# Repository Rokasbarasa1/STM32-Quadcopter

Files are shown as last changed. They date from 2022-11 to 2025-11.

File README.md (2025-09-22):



I am making a quadcopter from scratch (firmware including). This is the second step after my [Self balancing robot](https://github.com/Rokasbarasa1/ESP32-self-balancing-robot) project. It is still a work in progress, but a lot of the heavy lifting has already been done.

### Some features:
* Acro and Angle modes.
* GPS position hold flight mode (Work in progress).
* Altitude hold flight mode (Work in progress).
* Controled by my custom [Pi-pico based remote control](https://github.com/Rokasbarasa1/Pi-Pico-remote-control). 

### Sensors and hardware used for controller:
* Controller mcu - STM32F411
* Accelerometer + Gyro - MPU6050
* Magnetometer - MMC5603 (Used QMC5883 before)
* GPS - HGLRC M100 5883 (Used BN357 before)
* Barometer - MS5611 (Used BMP280 before)
* Radio link - RadioMaster RP1 2.4GHz ELRS (Work in progress)
* Debug Radio communication - NRF24l01
* Logging - [My custom STM32F411 based SD Logger](https://github.com/Rokasbarasa1/Logger). 

### Hardware of the drone itself:
* Motors - 4 x EMAX ECO II Series 2807 Motor
* ESC's - 4 x HGLRC 30amp 3-5S Dshot600 BLHeli_S 16.5 BB2 ESC (F-H-40 flashed with BlueJay 0.21.0V for BDshot600)
* Proppelers - 4 x HQProp DP 7x3.5x3 V1S 3 blade Propeller
* Battery - CNHL Black Series 3200mAh 14.8V 30C 4S (also used Turnigy 2200mAh 3S 25C)

# Latest flight video (January 2025)

Watch the video (https://www.youtube.com/watch?v=jI-Cl2vByNU)

# Pictures (Outdated)
Frame top
Frame bottom
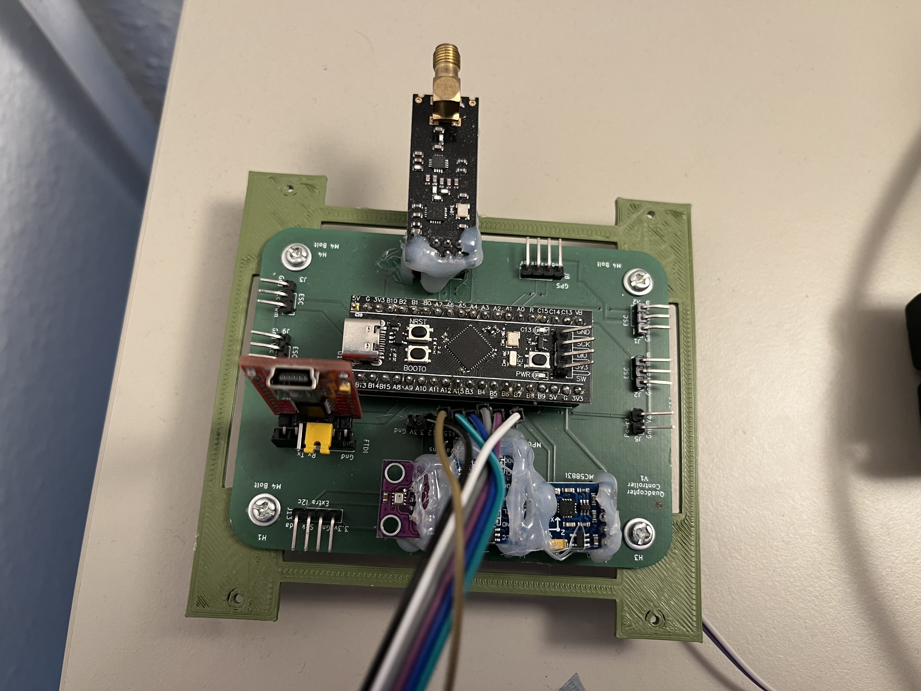
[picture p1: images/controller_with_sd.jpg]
Controller


### Checklist for going testing
* Drone frame
* Controller
* Controller antenna
* Propellers
* Sd card adapter
* Micro sd card
* Pliers 
* Wire cutters
* Screwdriver 
* Screwdriver bits
* Remote control
* Laptop
* Usb extension cable
* STM32 programmer
* Charged battery
* Battery checker

# Design documentation (work in progress)

## Code diagram

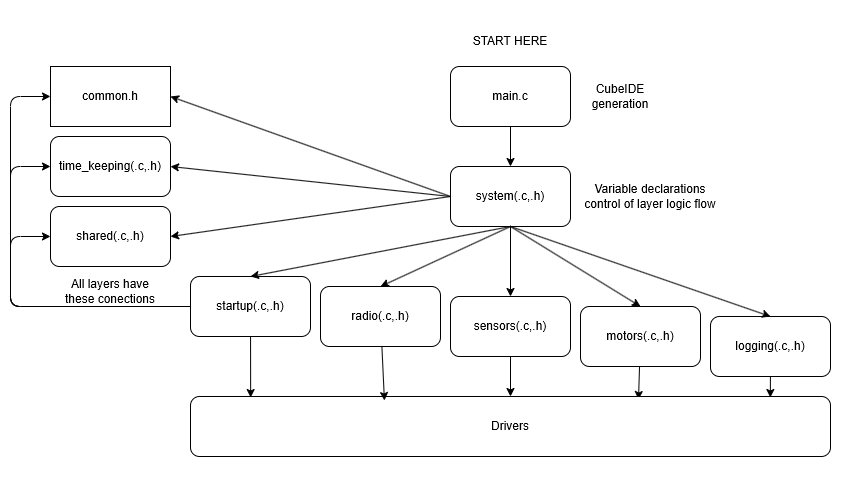
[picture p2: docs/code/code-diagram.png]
Code diagram


## Controller 

The controller is the main piece of the system. It is much more limited in what it can do than a normal computer, it is smaller, slower and resource constrained. So it cannot run a full GUI operating system. The good thing about them is that they are cheap and, depending on which one you get, just powerful enough to do interesting things. They are also cheap, I got mine for 7.28 USD. The microcontroller itself is just a chip on the breadboard. It is very self sufficient, sometimes you can just supply them stable power and they work fine. Like the attiny85 that just plugs into a breadboard. 

We need one that is more powerful than that so we will go with one called the STM32F411. ST(M)icroelectronics is the manufacturer, the 32 bit is how big data chunks the system can handle, and the F stands mainstream performance line of their chips, 411 is just a serial number for features. We dont really care about the features that much, it is maninstream so it will work for most things. 

I went with a ST microcontroller as it was one I had not used before. The chip on this one is very small so it is mounted on a pcb to seperate the tiny pins on the chip into big pins that we can use. The PCB that it is mounted on gives the microcontroller name blackpill because its a black pcb and its small. The pcb also has some extra features like voltage regulators to protect the chip, external oscillators to speed it up and leds to help us indicate status later. The pcb is so small that it lacks some quality of life features that a big pcb would have, like a programmer. The chip has to instead be programmed usng another product of ST called ST-link V2, which just converts a Usb interface to a programming interface for the stm32, it uses 4 pins to do that. This is negative of ST's products, other manufacturers dont have this problem with small pcb's, most of the time. The upside is you can debug the code with the same product, this is something that is painful on other microcontroller brands. The small form factor of the pcb is also very helpful for integrating the microcontroller into projects.

Each microcontroller manufacturer has their own "library" that abstracts the difficullt hardware drivers (HAL), on top of which the coding of the microcontroller can be done. In the case of the STM32 it is STM32Cube which lets you use C or C++ to write code for it. You can use Rust or anything else to write the code but then you are not using the manufacturers libraries and have to relly on open source. In my case I went with C as it is very simple and I can get great performance out of it. 

<!-- 
_The STM32F411 has a lot more GPIO than ESP32, which maybe has half of its pins unavailable and a bit more than the Pi-Pico on which a lot of the pins are grounds. Its also easier to mount on a breadboard than the ESP32._

_I hate the CubeMX code generation, feels like there is just junk in my repo. The alternative is really badly documented, to the point of needing to go into the library code to figure out how to use it. Feels like they skimped out on actual documentation to make you use the shitty code gen. Using the library code to figure something out is not easy either as there are multiple functions with similar names or functions that are depreceated. It always confusing to set anything up from scratch, like spi or i2c, there are so many functions that are supposed to do the exact same thing. By far the worst experiance of developing embededd software. Even fucking atmelavr felt like butter compared to this, though that might be a high bar in the embedded world. You cannot have development velocity in this ecosystem if you touch even a bit of the ST library. ESP32, Pi-pico and atmega are a lot better at this._

_Flashing the firmware on it is a lot easier though, in cases. If i was working on a breadboard, the Pi-pico would be a lot easier. When i made a protective cover for the controller part of the drone it was easy to press the pins of the programmer agains unsoldered holes of the pcb for programming. I did not have to fish for the 4 pins to attach too. This meant that sometimes the programming would not work, but overall it was a good experiance._

_For performance the STM32 is deffinetely not as fast as the ESP32, but it is fast enough, most of the performance is lost on sensor communication anyway._
-->

<!--
### Code design decisions

_The code looks not as a usual developers code looks like. I like having full names of the variables, no such bullshit as dT for delta time or whatever one letter variable. The same is for functions, full verbose names. I like to come back to old features and understand what is happenning. Lots of comments also._ 

_If there was a "Prettier" implementation for C (C code formaters are garbage, all of them) I would use it to enforce the same syntax everywhere, but there is not so there are gaps. I would love to enforce breaking of function variables if the developer has broken at least one, curly braces in line with for loops and if statments and functions.

_I tried to seperate the code into modules, of radio, data getting, motor control/pid and logging. They need to be moved to different files like controller/services/models architecture on backends, but at the moment it is just so much easier to have everything logic related in one file. In the future will be, main.c/business logic/drivers, with main.c only being able to reach drivers if it goes trough business logic. I come from full-stack development and we have much better understanding of code organization than embedded developers. The code will be seperated into seperate files once I am done with the project. I dont care about clean code, the functions will not be made 5 lines long._
-->

## Sensors drivers
To make our drone sense the world around it we need sensors. Based on the output of these sensors the code that i wrote in the microcontroller will make decisions and perform further actions to manipulate the environment it is in.

<!--
_A note about the sensor driver implementation. I continued the use of enums for defining the registers of the sensor and so on. Makes reading of the sensor code and even configuration of it a lot easier._

_Usage of macros for constant definitions is also done now. No more magic numbers, they have names now. Some pre division of these values is also done._
-->
### Supplying power to sensors
These sensors that we will talk about and hardware are meant to be powered some way, unless they have a battery on board them they have to have a physical connection to a power source. This is usually 2 wires, one for ground and one for most commonly 3.3V or 5V. A lot of the older snesors use 5V, these are usually the sensors made for the microcontroller called Arduino. These sensors need 5V because the old Arduino uses 5V logic(5V for a set bit and a 0V for a not set bit). If communication needs to be done to the sensor then there will always be a minimum of 2 wires or there can be more to accomodate different methods of sending or receiving information relating to the sensors. In the case where something has its own power source, and you know the power source or at least the interface that you will be using utilizes the voltage that is the same as you are using, then connecting the ground wire is enough. In fact if the device you are connecting to uses a different voltage than yours it is also safe to connect your ground to its ground. The important thing to match is the voltage lines, 5V, 12V, 15V.  

### Communcication to sensors
The sensors are just little microcontrollers in most cases, they have logic and interfaces that let the data be extracted from them digitally(toggling a single pin or more from 3.3v to 0V). There are sensors that are analog, but we are not using them, they are harder to work with. There are many methods of extracting the data out of sensors, these are called protocols. Each protocol has its advantages and disadvantages. Different combinations of, speed, wire count and complexity in setting it up. I will not be bothered to get into the details of how each protocol works as there are actual books for that. The best way to see how it works though is by getting thing called a "logic analyzer" and seeing for yourself how your hardware works.

#### I2C
I2C is one of the most convenient protocols to settup, it uses two wires, one for data and one for clock signal, it can also be chained to multiple sensors/device. Its fast enough and you can go above the recomended speeds if you believe in your hardware setup. I used I2C on my self-balacning robot project for sensors and it was fine. I did that again on this project and that was a mistake. You have to understand unless you are setting up something fancy to not have to do the communication to sensors synchronously, I2C can waste a lot of time by not being the fastest method.

I2c is very easy to setup though, and rarely ever causes problems. On the STM32 i did find that interrupts (will talk about these later) have to be disabled for the communication to not break. When it did break it would take 100ms to error out and continue with the program, essentially breaking the whole flow of the time sensitive program.

#### SPI
SPI is a lot harder to setup than I2c. The devices that can be communicated to using this have to have a slave select pin, that when 0V is applied to it means that the device is being communicated with. It also has 3 other pins, one for clock, one for data coming to slave and one for data coming to master. When you try to setup the hardware for a SPI connection, there is always something that just does not work. Its like having to plug in a usb, you always do it wrong way first. Sometimes the slaves/sensors have an extra pin that is also names similar to the slave select pin causing additonal confusion. The benefit of SPI is the speed it can reach, if you really need to be at the peak of performance then this is what you need. There are even variations of the protocol that use double or quadruple the pins amounts for the slave-master pins to multiply the transmission speed.

SPI is also a very simple protocol that you can even implement yourself. That cannot be said about I2C.

#### UART 
UART is the last protocol we actually care about and is one that is not normally used for sensors, but for transmitting text information or large amounts of data. It is also a very simple protocol, it uses 2 pins and does not use a clock pin. It  also cannot be chained like I2C and it is most importantly asynchronous by default. It is considered slower than the other protocols but it has benefits. It is reliable over long distances of wire and has recover mechanisms 

### I2C and sensors in general
For this communication we will use I2C. I2c is just a recipe (protocol) for what way to toggle the pins and in what order that both the controller trying to get the data (master) and the sensor (slave) understand and adhere to. There are other protoocls as well that the sensors support, like SPI, but I chose this one because it is easier to deal with. I2c uses only 4 wires, 2 for data. I2c is usually used for sensors or things that dont nescessarily need max speed in communication. You sacrifice speed for ease of communication.

### UART
Uart is another protocol for communication. It again uses 4 wires 

To do things with a sensor you need to read its datasheet. The most important part of which is the register map, it tells you where everything is stored and what register addresses you need to give to the sensor to read out the data from the registers. With i2c this often looks like sending the address of the register then reading the number of bytes you expect the data to be. Sometimes these sensors dont just automatically fill up their registers with data and you need to actually send commands that trigger actions that fill up populate those registers. Sometimes these commands just activate some special ability of the sensor. Thes sensors are almost always configurable in the same way also, by sending what register you want to fill up and then sending the bytes of data you want to put in that register. Configuring the sensor can be though of as having a wall of switches (the register map). There are as many rows of switches on it and the rows correspond to registers, each row has a number of switches that correspond to how large the register is in bits (most often its 8 bits). Each switch in the row does something, each one has a long description of its functionality in the datasheet. Some of the rows of switches you cannot manipulate as they are the ones storing the measurement that the sensor does, so the analogy falls appart there.

It should be noted that sensor data should never be taken as reliable data, the sensor data by default is always miscalibrated and has noise in it that makes judgements based on the data difficult. Each sensor type also has some problem that makes complex systems development difficult, but there are solutions to this, that we will talk about in sections "sensor fusion" and "filtering".

<!--
_I should have not used the I2c bus anymore in this project, for any of the sensors, its a bit too slow. I went above the recomended bus frequency though and reached 1.6 MHz but went down to 1.0 Mhz for stability just in case. That saved quite a of cpu time._
-->
# Gyro
The gyro can tell how fast the drone is rotating in each axis. If you tilt the drone 90 degrees to be on its side after it was standing flat on the ground and you do it immediately in one second the gyro will tell you that it degrees per second rotation is 90 on that axis you were rotating it around. To understand this, imagine a swing set attached to a metal pipe, the way the pipe is laying is some axis, lets say x, so the pipe is in line with the x axis. When you swing in the swing set you are really just rotating around the x axis of the pipe.

The gyro is the most important sensor for a drone. Depending on your requirements for the drone, it may be the only sensor you need, specifally for a mode control for the drone called acro mode. We will be implementing this mode of control but also more.
DRIFT

I am using the gyro on a sensor module called MPU6050. It is a common sensor, used on many drones. It actually has an accelerometer on it as well, but that is for later. The MPU6050 chip itself is mounted on a pcb that has voltage control stuff and power stabilization capacitors on it. This makes working with it easier, low risk of frying due to high voltage and it should be isolated from the power disturbances that can happen in an embedded system (these can just make the sensor not work very good). 

The sensor itself is configured by the code to be able to sense a max of 500 dps/s of rotation, which should be plenty for our drone if we dont plan to do spinny tricks in acro mode.

The gyro does have a problem. You may think if you keep summing the dps data over time, that you will get some data that tells you the orientation of the drone in 3D space, but that is not going to happen. The Gyro data is inherently noisy and if you sum it you will get values that drift over time. You can ease this noise issue by calibrating the gyro. Which is just reading maybe 1000 gyro values while sitting still and, finding the average gyro output value and then every time the you get the value out of the sensor you substract that average value from the data. This effectively removes some of the noise, but certainly not all of it. The next sensor will help deal with the noise issue.

### Accelerometer
The accelerometer can tell which way down is. You can imagine it like a a plank of wood in the air with a string tied to it and at the bottom of the string is a weight. As you move the the rotate the plank the string just keeps pointing to the ground. That is one property of the accelerometer, it can tell which way the ground is by displaying the force of gravity in G's split over 3 axies, x, y and z. So if the plank is at an angle to the ground, the G force will be split among the axies. If the plank is flat to the ground, only the z axis will have the value. If you make suddent movements and move some distance with the plank the weight will react to that and start to point away from down and will instead point slightly to the side. Using this you can sense when acceleration happens. This is where the analogy falls appart as the weigt will then have momentum, where as the real accelerometer will not be succeptible to that. When the acceleration stops the accelerometer will also stop being affected by it. board with weight

So now we know which way is down and we know if we are accelerating in some direction.

The accelerometer also has some problems. If we want to use the data in any way on something that moves and can control itself we will always have parasitic accelerations as its just picks up every movement and creates more acceleration data. The accelerometer also needs calibration, its calibration is in part similar to the gyro, but can go further. The same average value calibration can be done when the drone is flat (extremely flat, like bubble level flat in both axies), this gives you the deviation form actual gravity. If any other axis than z has average values of more than 0.01 then that needs to be substracted from them. If the z axis is not exactly 1.0 G then it needs to also be substracted or added to to make it 1.0. This is the first level of calibration. 

The second level is a bit more complicated, it can happen that when you rotate and try to isolate the axies (make the value only show on one axis) that value can be not exactly 1.0. If you were to rotate the drone around for 5 minutes straight without introducing ANY acceleration but gravity and logged all of that data and plotted it in a python 3 dimensional graph, you would see either a sphere or a ellipsoid(squished sphere). The shpere means youre accelerometer is probably good to go, but even a slight ellipsoid squish means its bad. To fix this type of problem we need to use linear algebra and use matrix multiplications to transform the data into the sphere. For this I used a software called magneto12, I give it the raw values of the accelerometer and it calculates me how the modifications to the values. These calibrations are then applied every single tiem the acceleration data is gotten.

Sphere
ellipsoid

The accelerometer combined with the gyro though solves this issue. We will talk more about this later, but gyro+accelerometer can give us accurate data on our orientation for axies x and y, but not z. This data is enough to make a drone that has a flight mode called angle mode. The next sensor will solve that problem of the z axis.

The accelerometer we will be using is on the same chip as the gyro, the MPU6050. We will use the 2G range of readings for the accelerometer. Having a lower g value capture means there is more bits of data left for higher resolution value storage (higher resolution means you just have more digits after the decimal).

### Magnetometer
The magnetometer can sense the magnetic field of the earth, it gives these readings in micro teslas in 3 axies. That is as much as I know about how it works. The magnetometer can be used to always know in which direction is north, acting like a compass. You can use the relation to north to figure out which way you are facing or at least have a reference to where you were facing and which way you are facing now. The magnetometer is also essential if you want to use a GPS.

The magnetometer has some problems though, its data can be disturbed by magnetic fields of magnets and various metals. To use it, you need to always calibrate it, otherwise the data is useless. The calibration method is similar to the accelerometer calibration part 2. You collect a lot of data by rotating the drone in the air repeatedly, all kinds of loops, then you plug that inot magneto12 and you get two calibrations. A "hard-iron" calibration with 3 values and a "soft-iron" calibraiton with 9 values, really just a modified identity matrix. The "hard-iron" distortion is caused by magnets and the  calibration is just a offset of the value to center it around 0, similar to the gyro calibration. The "soft-iron" distortion is caused by various metals being around the sensor, it can also be characterized by the data not looking like a sphere but like a ellipsoid, just like the accelerometer one. It can also happen that you see a pancake in the "soft-iron" calibration, that means your sensor is not good and should be replaced, more on that later. All of these calibrations ideally have to be done outside in nature, far away from any disturbances. It is also very important that the drone is fully assembled when calibratin as each drone component can have some disturbance to the magnetometer.

I originally went with the QMC5883L magnetometer, it had a lot of problems with pancake graphs, but the ocasional one worked ok. When i started making my quadcopter I ripped the only working one that i had out of my self-balancing drone and it also turned into pancake. Eventually i had to get rid of all of them and just get a new sensor. I got the AdaFruit MMC5603 to replace it, origianlly I was really afraid that something was going to be wrong with it as the sensor chip was so tiny, but it was wrong and the sensor has so many more features. It is able to test the values it puts out itself and determine if something is wrong, set a data fetching rate, it can degauss itself which is amazing. Its such a great little sensor, it solves all of the problems i had with the magnetometers.

### UART

### GPS
The GPS is technically not a sensor but a receiver antena for sattalite signals, but I do like to call it a sensor. It picks up signals sent by sattalites of different constelations like GPS or Gallileo. It then uses the signals it receives and math to compute where it is on earth. The more sattalites it has the more accurate the calculation is. It outputs a lot of different data, but we primarilly care about about latitude, longitude, sattalite count and fix quality. The latitude is the vertical coordinate on the globe it increases or decreases when you go north or south, like y axis on a graph. The longitude is the horizontal coordinate and changes value when you go west or east, like x axis on a graph. The longitude is a special case, it is not linear like the latitude, it increases in precision when you go further away form the equator. This makes a bit difficult to work with as the code needs to use the linearized version of longitude, but to display the data you need to see it non linearly. The sattalite count is important to know the quality of data that is being delivered, a sattalite number of 10 or above is good quality. The fix type is a lower bar for quality, if the fix type is "3D" it is good enough quality to do some really bad gps position tracking or holding.

The gps can be used for a lot of things, but we are going to use it for position hold and maybe later for waypoint following.

### Barometer
The barometer can tell you how dense the air is. If you lift the drone up it will show lower pressure and if you lower it it will have higher pressure. The drone can sense the change in pressure and then convert that pressure change in to actual measurable change in altitude. This is essential for altitude hold functionality. 

There are problems though, a drone has propellers and propellers can generate wind and low pressure, the barometer can pick up this pressure change and provide fake data that will make the drone think the altitude is changing quicker that expected. Dealing with this is difficult. I have not progreessed far in this area yet, but I have tried to isolate the the sensor using foam and tape so cross wind cannot blow over it and aid can only come in from one side and the result was no improvement. Still some work left to be done

The sensor I chose first was the BMP280, which is a fine sensor and worked fine but I felt that it was not precise enough. I switched it out for the MS5611 which is widely used due to its accuracy. Barometers often come bundled with temperature sensors and even humidity sensors in some cases. These additional sensors aid in altitude calculations as then everything about the atmosphere that is important to altitude can can be sensed.

Calibration for barometers is done in the factory they were made in. The sensors registers hold the calibration data which is read on sensor initialization and applied once data is gotten. The MS5611 sensor is one of those sensors which you have to tell to start taking a data sample of either temperature or pressure and wait a bit until the data is ready. In our case we alternate between getting the temperature and pressure to have the most accurate altitude measurement in the end.

The altitude calculation can be done as an absolute altitude using formula to determine the current altitude from numbers purely. This altitude calculation is often best when setting a initial altitude by manually if it is known. This is good for devices that are intended to measure altitude in a human understandable way. The other options sampling pressure, setting that as the reference pressure and then always measuring the changes in altitude based on how far away it goes off the reference. This is effectively setting the sea level to be at the current pressure. It is useful for applications where you just want to know which way the altitude changed and that it is stable. This second option is what we use for our drone.

## Other hardware 

### A note about powering of hardware 
When i said that the 

### SPI
We talked about I2C before and how it is a protoco for communication, there is another one called

### Debug Radio
To actually communicate to the drone you need something that can pick up wireless signals. When I was making my self-balancing robot I create a remote control that had a radio transceiver(can send and receive radio signals) on it. So i chose to use the same setup on the drone.

A radio module is just like one of the sensors it communicates to the  

### Axies
Explain X Y and Z. 

BREADBOARD

### Old todo lists i will remove later

TODO after test 1:
* X Take off testing equipment as drone is too heavy to fly.
* X Uncomment second axis stabilization

TODO after test 2:
* X fix stuttering issue with motors. I think it is from receiving too little radio signals
* X figure out how to make screw nuts not undo themselves. Make the whole thing more rigid.
* X maybe upgrade to the extended range radio sensor
* X Make the robot turn off if it gets to an angle of like 45 degrees as that is not helping it hover

TODO after test 3:
* X Fix issues with remote restarting and roll joystick not making contact with pins.
* X Fix quadcopter event loop lag. Improve refresh rate of robot
* ! figure out how to use integral without super windup
* X remove comments from both remote and quadcopter.
* X add loop timing to remote to have constant refresh rate
* X Implement logging to sd card and log in a format that can be understood by something like betaflight blackbox analyzer
* X Make sure the motors never stop spinning at even at the lowest setting when controlled by the remote. This will help responsiveness.

TODO after test 4:
* ! Add blackbox logging for gps data
* X Find out how to adjust what pwm frequency the esc accepts and change it from 50Hz to as fast as possible.
* X The radio module caches the data sent durring the boot proccess of the quadcopter. Make sure the data is deleted before it gets to the pid loop as it is dangerous.
* X Recalibrate accelerometer because it was moved and reglued.

TODO after test 5:
* X Tie down new escs like the old ones were
* X Make sure the motor screws don't undo from vibrations
* X Mark the front and back of the drone
* ! Fix issues with magnetometer
* X Fix blackbox log roll log being opposite
* X Reduce angle of attack for pitch and roll

TODO after test 7:
* ! Fix issues with blackbox logging showing wrong motors spinning and wrong pitch and rol. All of them either inverted or showing up on the wrong motor.
* ! Find a new more reliable magnetometer
* X Attach an FPV camera for better orientation and control while flying.

TODO after test 8 (Crashed and broke a rotor leg):
* X Print new rotor leg parts
* X Resolder cut ESC wires
* X Flip degrees per second yaw control application to motors and reduce the gain.

TODO after test 9:
* ! Continue doing small tests to see which way the robot is leaning with no pitch or roll inputs to calibrate the accelerometer
* X Add accelerometer calibration tweaking to the remote control so the drone does not have to be reflashed every time
* ! Consider switching to the kalman filter for better sensor data

Test 10
The new feature of the remote control being able to change the accelerometer offsets was really good. I managed to get a general direction in which it needed to be adjusted, it always leaned right and a bit forward. I was not able to adjust it perfectly though as i ran into issues of my pid settings just not being good enough, P and D are no longer enough to keep good balance. The new flight mode did not work as expected, i set it lower than what is generally expected from it and i did see that it was not enough, i needed to make a big demand of 70 cm for it to star rising a bit, which was not good. Need to have more confidence in it to not go flying somewhere, but possibly try it more after i figure out balance on the mode 0 balance. Low pass filtering of the gyro and accelerometer did not really have a negative impact on the quadcopter. Tried playing around more with the integral with a bit of success in lowering the oscillation of the drone when balancing. Need to continue tests on a very flat surface next as moderately level ground is not enough anymore. The beta in the 

TODO after test 10
* Do more tests in flight mode 0 with integral and when a better balance PID is found adjust accelerometer offsets again.
* Add a note in the remote control accelerometer calibration screens what the impact of the calibration will be, like - +X = Pitch forward and so on.
* Compare to other quadcopter projects to see what i am missing to make things better.

Test 11
Realized that offsetting the actual accelerometer calibrations might not be the best way to fix the quadcopter balance point. Tried implementing a degrees offset for the pitch and roll of accelerometer but ran into issues of feedback loops once the offset is applied, making one or more motors spin faster and faster when idle on the ground until they shut off. Meaning that the gyro_degrees is affected in a feedback loop. (The feedback loop turned out to be related to the mpu6050 outputs of acceleration and gyro freezing)

TODO after test 11
* Figure out problem with feedback loop of offset degrees
* Replace MPU6050 with new sensor as this one is getting frozen sometimes. It is fine to use for testing now, but for extended flights in the future it will fall from the sky.

Test 12
I did some more tests and i found out that there is a problem with using calibration and filtering. If calibration was done on data that was not filtered and then the actual data used is the filtered one, the effect is that the calibration is useless. I have to either apply filtering on the sensor hardware level or use filtering everywhere in software including when calibration is done. Durring testing i saw that the gyro values post calibration were a constant 3 degrees/s which made half of the flight test useless as the battery was half drained. 

I also found that that the motor and prop vibrations really do affect the sensor readings a lot, i am surprised it even hovers a bit after looking at them at 40% throttle.

TODO after test 12
* ! Add material dampening of vibration
* ! Improve software filtering to remove what vibration was not already removed by material dampening.
* ! Test vibrations with fresh propellers.

Test 13
Tested the new low pass filtering on the drone. It worked very good at the 45Hz frequency setting, not so good at 22Hz or 10Hz with significant delay in response being visible. Did more tests on the yaw control functionality, it works very well now but there is a big drop in throttle when yawing with at a fast rate. The altitude hold functionality in flight mode 1 works better now but is still no good as i still need to put the throttle stick to 75% for it to do anything and lift off it does not keep the altitude at a neutral position. The balance correction is now easier with the low-pass filter but it still needs some work to find the sweet spot.

TODO after test 13
* ! Find out if the yaw control throttle issue with altitude could be solved or if that is just because my quadcopter does not have enough power in to keep altitude with two motors.
* ! Improve the offsets more on the next test.
* ! Find out why the altitude is not working so good.

Test 14
Got a better balance point but when testing the altitude hold broke one of the legs.

Test 15
Dialed in the altitude hold settings for PID, the quadcopter now holds altitude relatively well, but as it struggles to find a level offset it is not good to improve it more at the moment. The offsets still change a lot even with a low pass filter on, need to invest more in flight-controller dampening.

Test 16
Mounted new motors and tested them. Much less vibration as can be seen in the vibration profile for them. The quadcopter flies a bit better, but not as much change as i though it would have. I tried my best to balance it so it does not drift and got closer than the other motors, but did not get results that are much better. I am no longer even sure that this is a goal worth doing more tests for, and maybe i should just get the best stabilization i can and move on to perfecting the altitude hold and gps hold.

I tested it again the same day. Managed to improve the altitude hold functionality, by raising the integral gain 12 times I sped up the time it takes for it to charge up, so it reacts faster from ground launch. An issue is that raising the integral gain to charge it faster makes the integral give some overshoot to the vertical velocity target, for this i raised the proportional by 0.2 and got it to control a bit. Further testing is needed.

I did notice that with the new prop and motor combo the quadcopter does not have as much battery, so it means it is less efficient. This is expected as the propellers are smaller. I have also found that the new propellers are more durable than the ones i had before, maybe the decreased tip speed, material and shape of the tips plays a role in that. The quadcopter feels more loose with the new propellers, and that is not necessarily a good thing.

TODO after test 16
* ! Tighten all the nuts on the legs
* ! Find out why when gps is enabled the flight controller starts having a 140ms delay in sensor readings in I2C after the thing being on for a couple of minutes. 

Test 17

I have hit a dead end in testing. The drone is not supposed to handle this bad, vibration has been eliminated. I believe i am missing something big in regards to PID. I have seen others implement acro mode first and then feed that to implement angle mode. I am going to try to do the same as i have planned to implement acro mode anyway.

Test 18

I was correct in thinking something was missing. As soon as i started testing with pid as angle mode -> acro mode -> motors things started to work great. The drone now balances a lot better in angle mode and is very easy to control compared to before. Acro mode works ok, i can see some wobble as it wants to settle down to to a angular rate, which means there is more tunning to do. The next step will be to get the sd card blackbox logger working again, by fixing the hardware problem it has. Using the logger I will be able to see how it responds to setpoints over many different pid values for the acro mode and in that way i can figure out which one fits it best.

TODO after test 18
* X Fix the logger hardware problem.
* X Add more details to the betaflight log about the settings of the quadcopter, so that it allows the data to be analyzed more.
* X Make it so that when PID settings are changes, the quadcopter starts writing a new blackbox log file.
* X If the quadcopter starts a new log file it has to add the ending to the old one, so that opening it is easier on the computer.
* X Tune the blackbox log to the point that the log corresponds correctly to drone orientations
* ! Perform tests as in Chris Rossers's video on PID tunning.
* X Fix broken legs.
* ! Try flashing BlueJay to the ESC's to have rpm data from the esc's

Fix roll and pitch joystick
Fix scaling of ALL degree values
Fix right side motors not showing.
The fft graphs don't show throttle vs frequency noise plot. No Throttle detected

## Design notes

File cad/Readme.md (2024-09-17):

# Printer settings for parts

Rotor leg - 100 % infill, 0.3 mm layer height. Everything else default on my Artillery Hornet
Body - 45 % infill, 0.2 mm layer height. 4 layer walls. Top/Bottom thickness 1.0 mm. Grid infill
Roto leg supports - 20 % infill, 0.3 mm layer height. 7 layer walls. Top/Bottom thickness 1.0 mm. Cubic infill

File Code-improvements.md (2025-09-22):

* Split driver code into core components and platform specific components. Core is the logic of the driver and platform specific is i2c and spi stuff for esp32, stm32, pi-pico.

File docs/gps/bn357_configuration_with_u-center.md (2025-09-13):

# Configuring with u-center V1
I have not implemented the configuration of the GPS in code as that is a bunch of UART commands and switching to one baud rate and then switching back... a pain in the ass.

Instead the configuration should be done once on the UBlox u-center V1 software.

## Steps:

1. Hook up the GPS module to a FTDI chip and connect it to your computer. Power it with 3.3V, it says it needs 5V but in all my tests the 5V modules can be powered perfectly fine with 3.3V

2. Open U-center

3. Connect to the GPS module in U-center on the correct COM port.

4. Wait for the GPS module to acquire some sattalites and get at least a 3D fix mode.

4. Disable all non needed data coming from the GPS. Only signals that are needed are GNGGA and GNGSA. If the data does not start with GN then you need to enable more satellite constellations.

To find what data is sent:<br/>
View -> Messages View -> Non grayed out are the one
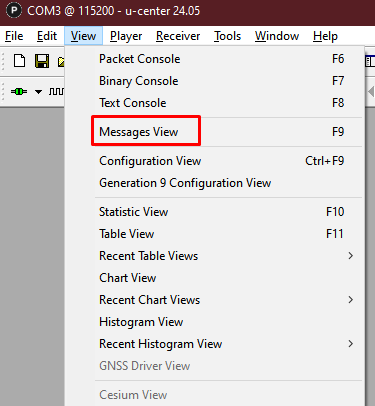
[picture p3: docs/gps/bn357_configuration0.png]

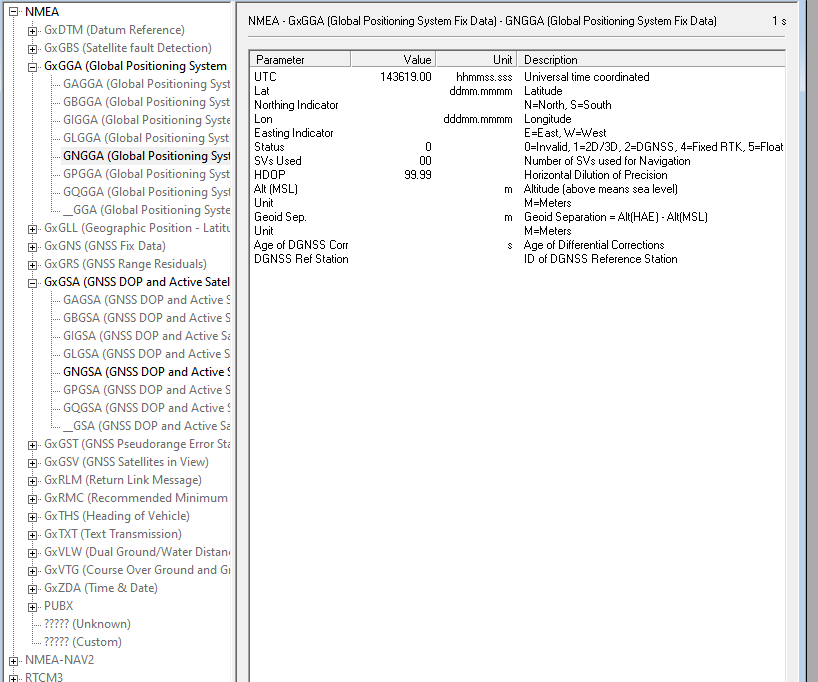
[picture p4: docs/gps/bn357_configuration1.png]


The black text data is what you are getting.

To disable or enable some of these:<br/>
View -> Messages View -> UBX -> CFG - > MSG
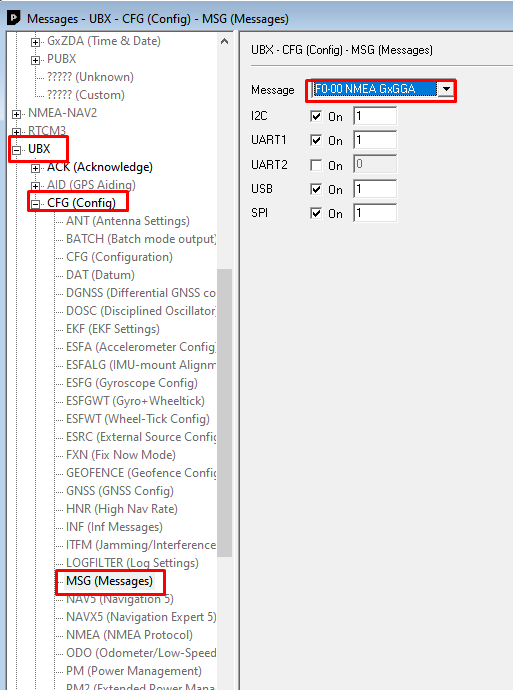
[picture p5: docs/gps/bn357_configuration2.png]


Now disable all the ones you have but don't want, compare to what you have in the message view. I want GNGGA and GNGSA to be left on.
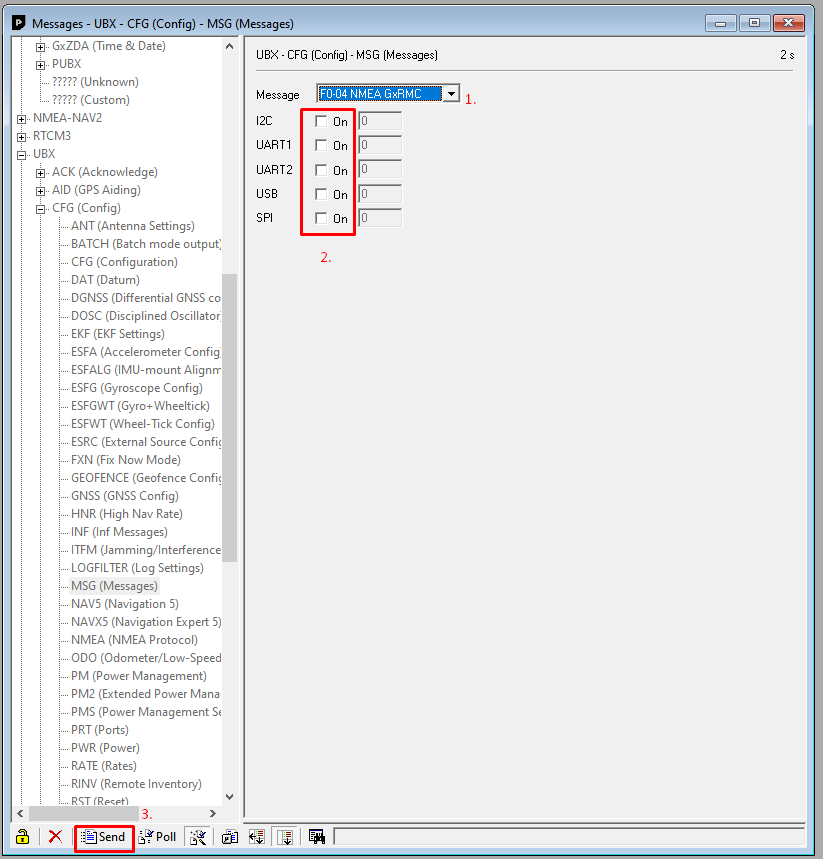
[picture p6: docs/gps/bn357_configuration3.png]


5. Save the disabled messages to GPS long term storage.

View -> Messages View -> UBX -> CFG - > CFG
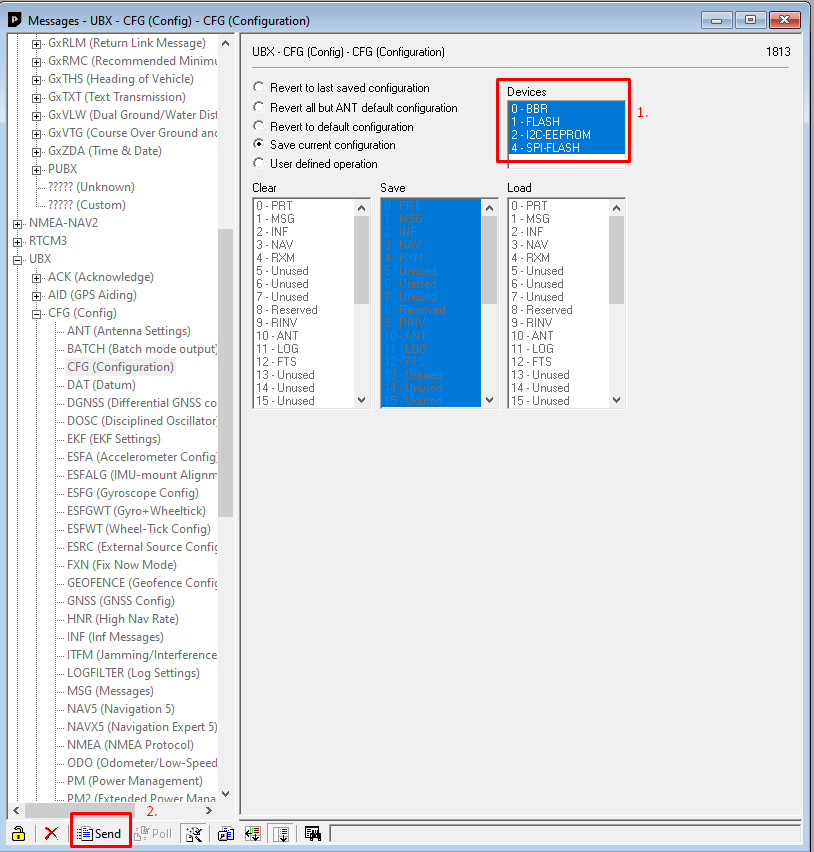
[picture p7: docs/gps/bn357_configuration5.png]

Check all devices with CTRL+Left click and then click save

6. Change the baud rate 
View -> Messages View -> UBX -> CFG - > PRT
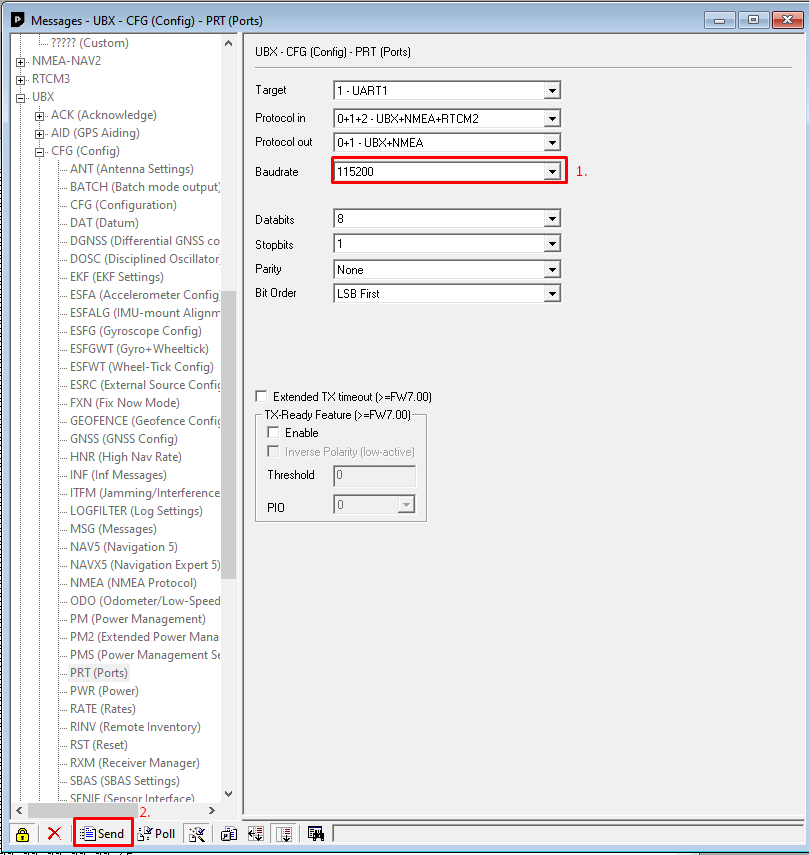
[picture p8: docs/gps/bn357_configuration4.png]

Set the baud rate to 115200

7. Reconnect to the GPS module with the different baud rate setting.

8. Save the new baud rate to long term storage.

9. Increase the frequency of data sent
View -> Messages View -> UBX -> CFG - > RATE
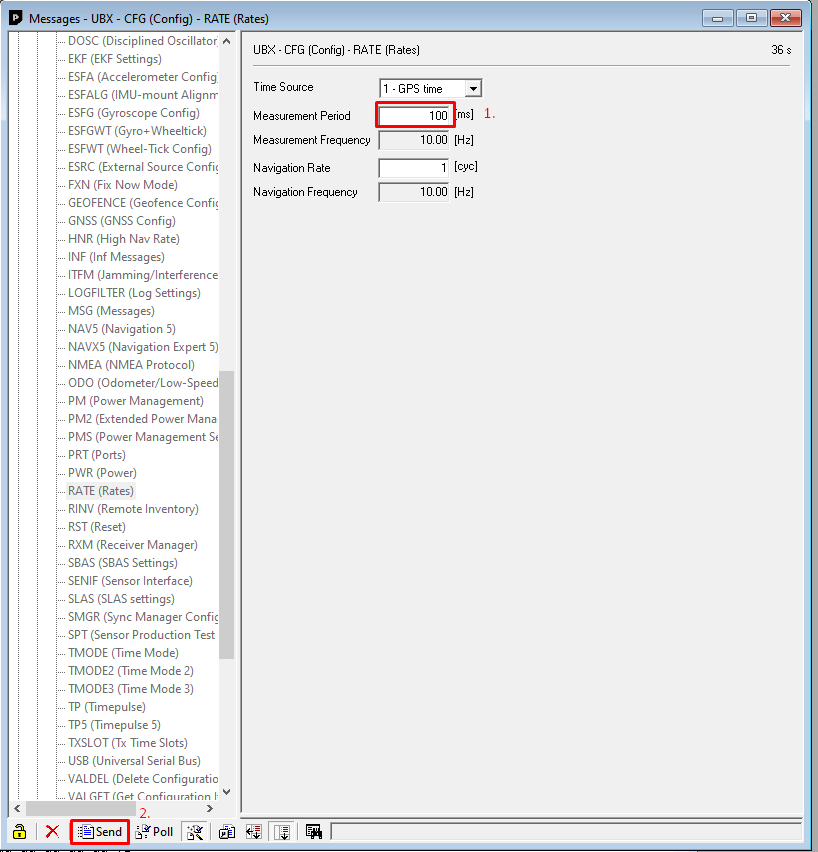
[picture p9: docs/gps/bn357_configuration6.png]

Set the measurement period to 100 ms which is effectively data at 10Hz

10. Save the new refresh rate to long term storage.

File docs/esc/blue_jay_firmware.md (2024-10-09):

# How do flash BlueJay without a FC

I used a F3 discovery board that i had from a long time ago, flashed Betaflight on it and used it as a fake flightcontroller that acts as a middleman to the ESC's. I flashed them one at a time from the same pin.

You do not need a F3 discovery. A F4 Discovery or a blackpill F411 with a working USB port will work. For the F3 i had to look at outdated releases to find a firmware that was still compatible with it. F411 is still well supported. I used Esc-configuration site. Worked very good. I used betaflight_4.0.6 for the F3 Discovery

Do not try to use Arduino for this. I tried to use BlHeliSuite16 to flash the firmware but the software kept complaining if i tired to flash BlueJay firmware. It just does not work.

Betaflight guide for F3: https://betaflight.com/docs/wiki/boards/archive/stm32discovery
Guide to Bluejay: https://www.youtube.com/watch?v=yEDhnBUFQNI&t=350s

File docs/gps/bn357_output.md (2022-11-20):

## **For more info lookup NEMA 0183 standart**
# First two letters meaning - NMEA Message Talker ID
- **GPS, SBAS, QZSS** -P G
- **GLONASS russian** - GL 
- **GALILEO european** - GA
- **BEIDOU chinese** - GB
- **Any combination of GNSS** - GN

# Letters after first two

- **$xxBOD** – Bearing, origin to destination
- **$xxBWC** – Bearing and distance to waypoint, great circle
- **$xxGGA** – Global Positioning System Fix Data
- **$xxGLL** – Geographic position, latitude / longitude
- **$xxGSA** – GPS DOP and active satellites 
- **$xxGSV** – GPS Satellites in view
- **$xxHDT** – Heading, True
- **$xxR00** – List of waypoints in currently active route
- **$xxRMA** – Recommended minimum specific Loran-C data
- **$xxRMB** – Recommended minimum navigation info
- **$xxRMC** – Recommended minimum specific GPS/Transit data
- **$xxRTE** – Routes
- **$xxTRF** – Transit Fix Data
- **$xxSTN** – Multiple Data ID
- **$xxVBW** – Dual Ground / Water Speed
- **$xxVTG** – Track made good and ground speed
- **$xxWPL** – Waypoint location
- **$xxXTE** – Cross-track error, Measured
- **$xxZDA** – Date & Time

# Example parsing

<p>$GNGGA,182459.00,5551.75853,N,00950.61588,E,1,05,5.31,-14.8,M,43.4,M,,*56</p>

- GNGGA         - Any GNSS satellite, sending global positioning system fix data
- 182459.00     - Time 
- 5551.75853,N  - Longitude. N 55°51'75.853''       DMS (degrees, minutes, seconds)*
- 00950.61588,E - Latitude. E 9°50'61.588''         DMS (degrees, minutes, seconds)*
- 1             - Quality of gps: 0 - invalid, 1 - standard GPS, 2 - differential GPS, 6 - estimated fix
- 05            - Satellites visible
- 5.31          - HDOP horizontal dilution of precision
- -14.8         - altitude
- M             - Units of altitude
- 43.4          - Geoid seperation
- *56           - Checksum

# Rest of the data
<p>$GNGGA,182459.00,5551.75853,N,00950.61588,E,1,05,5.31,-14.8,M,43.4,M,,*56</p>
<p>$GNRMC,182459.00,A,5551.75853,N,00950.61588,E,0.247,,131122,,,A*68</p>
<p>$GNVTG,,T,,M,0.247,N,0.457,K,A*3A</p>
<p>$GNGGA,182459.00,5551.75853,N,00950.61588,E,1,05,5.31,-14.8,M,43.4,M,,*56</p>
<p>$GNGSA,A,3,32,22,25,,,,,,,,,,9.21,5.31,7.53*16</p>
<p>$GNGSA,A,3,82,71,,,,,,,,,,,9.21,5.31,7.53*1C</p>
<p>$GPGSV,3,1,10,03,07,003,,06,26,078,,17,02,036,,19,28,049,*7E</p>
<p>$GPGSV,3,2,10,22,27,313,25,24,44,147,,25,54,256,26,29,08,201,19*75</p>
<p>$GPGSV,3,3,10,31,05,303,,32,40,280,26*74</p>
<p>$GLGSV,3,1,09,70,27,257,15,71,31,316,29,72,07,359,,73,14,285,19*68</p>
<p>$GLGSV,3,2,09,78,01,099,,79,50,087,13,81,50,092,,82,26,151,22*69</p>
<p>$GLGSV,3,3,09,88,25,028,*51</p>
<p>$GNGLL,5551.75853,N,00950.61588,E,182459.00,A,A*72</p>
<p>$GNRMC,182500.00,A,5551.75843,N,00950.61576,E,0.856,,131122,,,A*6F</p>
<p>$GNVTG,,T,,M,0.856,N,1.586,K,A*3C</p>
<p>$GNGGA,182500.00,5551.75843,N,00950.61576,E,1,05,5.31,-14.6,M,43.4,M,,*55</p>
<p>$GNGSA,A,3,32,22,25,,,,,,,,,,9.21,5.31,7.52*17</p>
<p>$GNGSA,A,3,82,71,,,,,,,,,,,9.21,5.31,7.52*1D</p>
<p>$GPGSV,3,1,10,03,07,003,,06,26,078,,17,02,036,,19,28,049,*7E</p>
<p>$GPGSV,3,2,10,22,27,313,25,24,44,147,,25,54,256,27,29,08,201,20*7E</p>
<p>$GPGSV,3,3,10,31,05,303,,32,40,280,26*74</p>
<p>$GLGSV,3,1,09,70,27,257,14,71,31,316,29,72,07,359,,73,14,285,19*69</p>
<p>$GLGSV,3,2,09,78,01,099,,79,50,087,12,81,50,092,,82,26,151,22*68</p>
<p>$GLGSV,3,3,09,88,25,028,*51</p>
<p>$GNGLL,5551.75843,N,00950.61576,E,182500.00,A,A*7F</p>
<p>$GNRMC,182501.00,A,5551.75853,N,00950.61573,E,0.817,,131122,,,A*6F</p>
<p>$GNVTG,,T,,M,0.817,N,1.512,K,A*34</p>
<p>$GNGGA,182501.00,5551.75853,N,00950.61573,E,1,05,5.31,-14.4,M,43.4,M,,*52</p>
<p>$GNGSA,A,3,32,22,25,,,,,,,,,,9.20,5.31,7.52*16</p>
<p>$GNGSA,A,3,82,71,,,,,,,,,,,9.20,5.31,7.52*1C</p>
<p>$GPGSV,3,1,10,03,07,003,,06,26,078,,17,02,036,,19,28,049,*7E</p>
<p>$GPGSV,3,2,10,22,27,313,25,24,44,147,,25,54,256,26,29,08,201,19*75</p>
<p>$GPGSV,3,3,10,31,05,303,,32,40,280,26*74</p>
<p>$GLGSV,3,1,09,70,27,257,12,71,31,316,29,72,07,359,,73,14,285,19*6F</p>
<p>$GLGSV,3,2,09,78,01,099,,79,50,087,13,81,50,092,,82,26,151,22*69</p>
<p>$GLGSV,3,3,09,88,25,028,*51</p>
<p>$GNGLL,5551.75853,N,00950.61573,E,182501.00,A,A*7A</p>
<p>$GNRMC,182502.00,A,5551.75849,N,00950.61628,E,0.293,,131122,,,A*6C</p>
<p>$GNVTG,,T,,M,0.293,N,0.542,K,A*36</p>
<p>$GNGGA,182502.00,5551.75849,N,00950.61628,E,1,05,5.31,-14.5,M,43.4,M,,*56</p>
<p>$GNGSA,A,3,32,22,25,,,,,,,,,,9.20,5.31,7.51*15</p>
<p>$GNGSA,A,3,82,71,,,,,,,,,,,9.20,5.31,7.51*1F</p>
<p>$GPGSV,3,1,10,03,07,003,,06,26,078,,17,02,036,,19,28,049,*7E</p>
<p>$GPGSV,3,2,10,22,27,313,24,24,44,147,,25,54,256,26,29,08,201,19*74</p>
<p>$GPGSV,3,3,10,31,05,303,,32,40,280,26*74</p>
<p>$GLGSV,3,1,09,70,27,257,11,71,31,316,29,72,07,359,,73,14,285,19*6C</p>
<p>$GLGSV,3,2,09,78,01,099,,79,50,087,14,81,50,092,,82,26,151,</p>

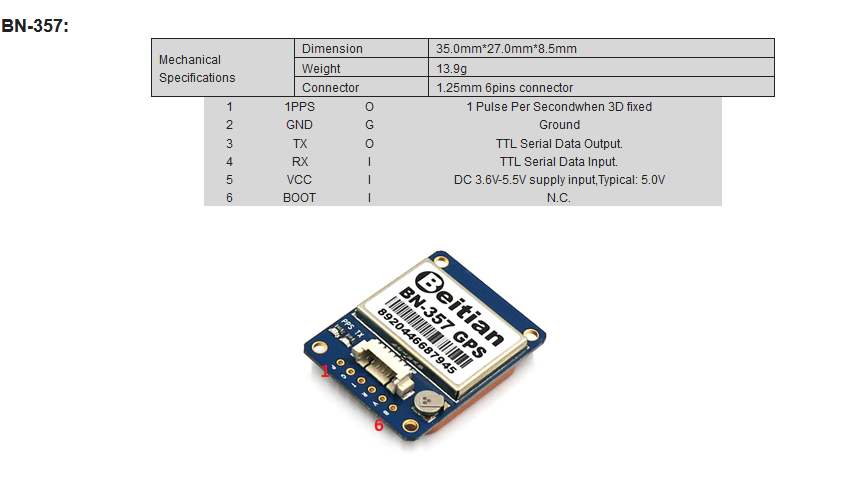
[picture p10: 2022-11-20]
docs/gps/bn357_pinout.png

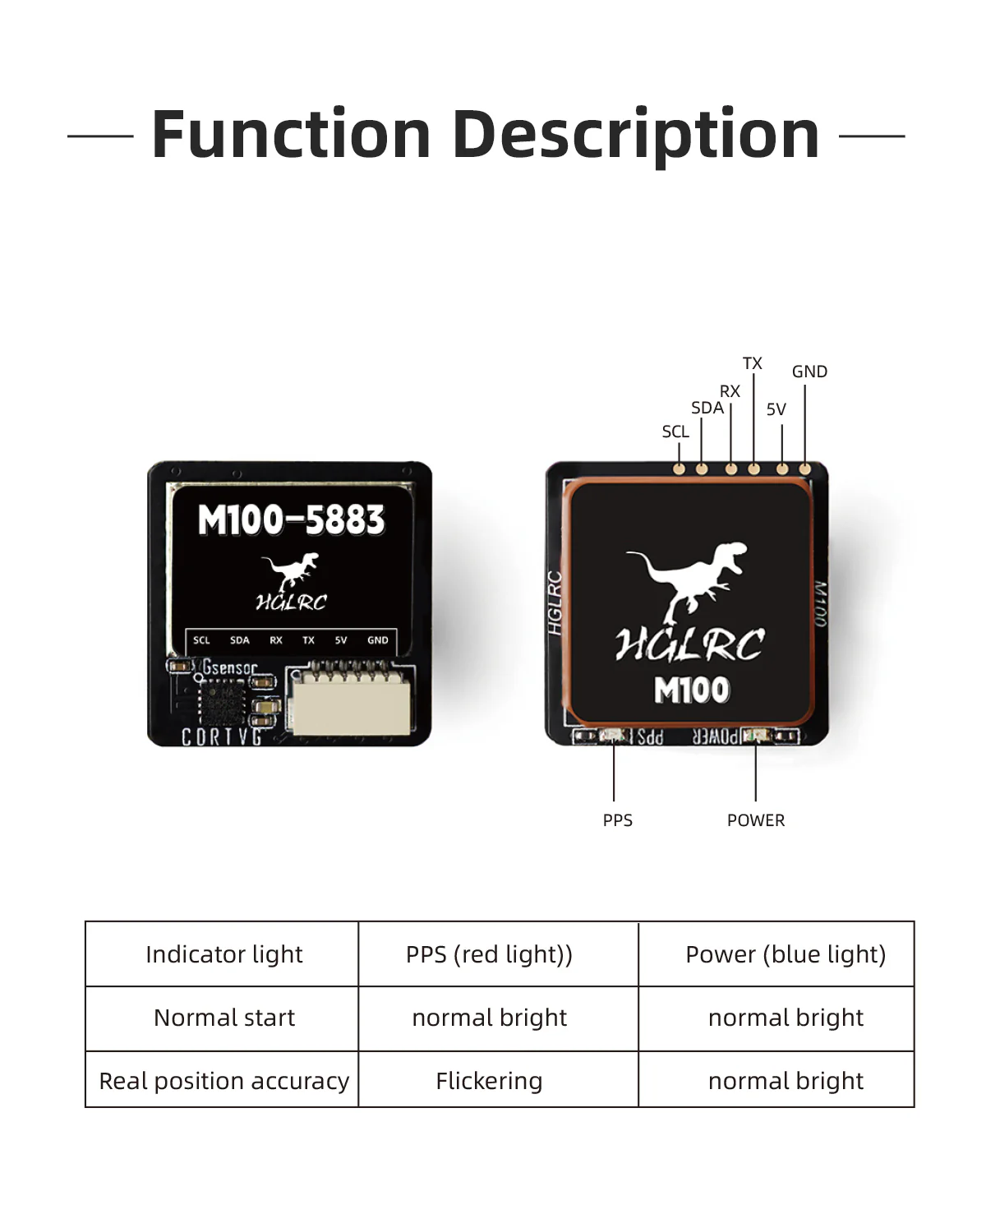
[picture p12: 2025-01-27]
docs/gps/hglrc_m100_5883_pinout.webp

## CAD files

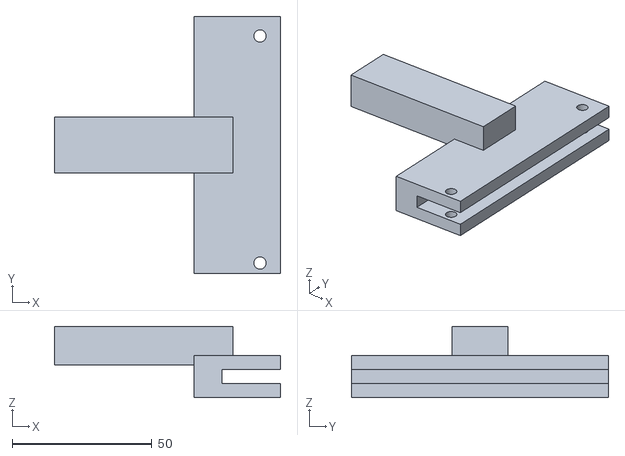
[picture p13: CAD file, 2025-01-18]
cad/failed_testing_equipment/test_arm_r.stl
81.0 x 92.0 x 25.5

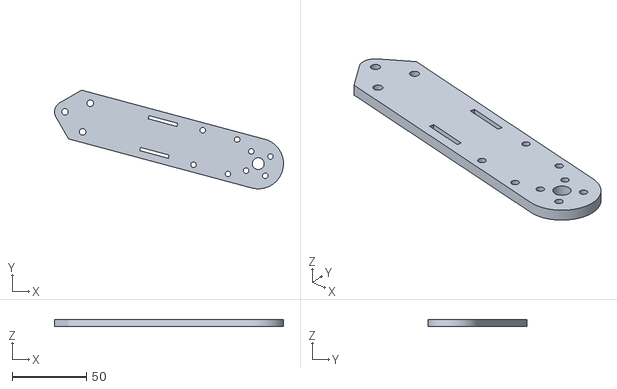
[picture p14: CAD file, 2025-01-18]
cad/motor_arm.stl
154.5 x 66.6 x 5.00

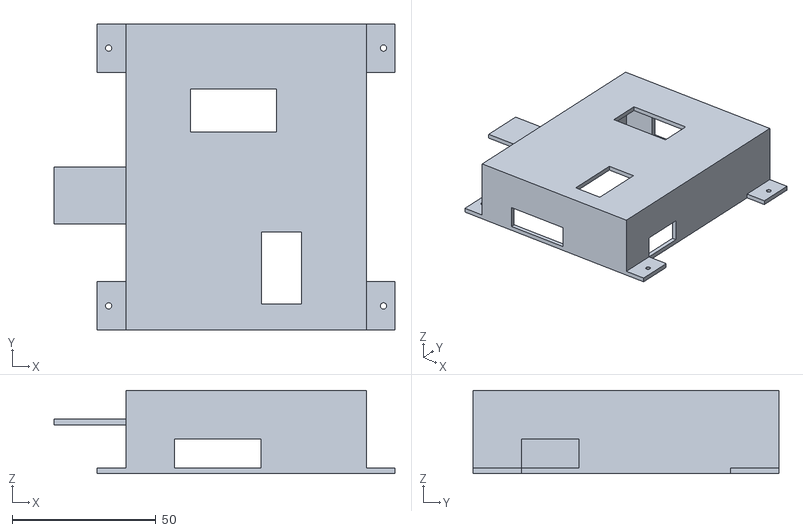
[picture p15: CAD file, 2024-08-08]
cad/case_top.stl
118.7 x 106.5 x 29.0

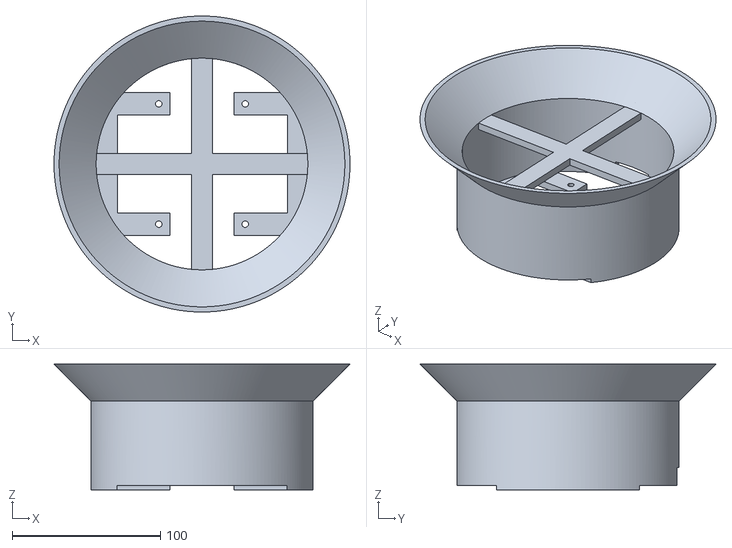
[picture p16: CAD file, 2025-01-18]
cad/failed_testing_equipment/hand_guard.stl
200.0 x 200.0 x 85.0

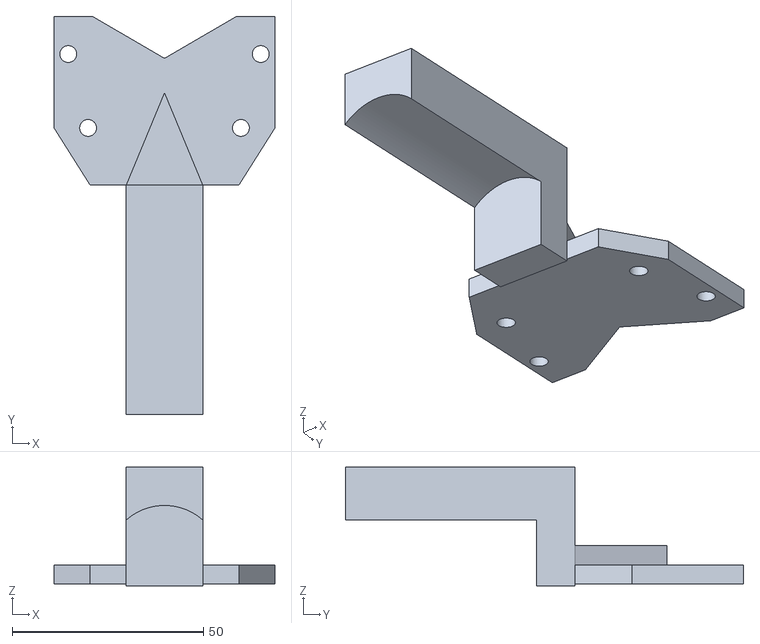
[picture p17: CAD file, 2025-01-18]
cad/failed_testing_equipment/test_arm_f.stl
57.8 x 104.1 x 31.0

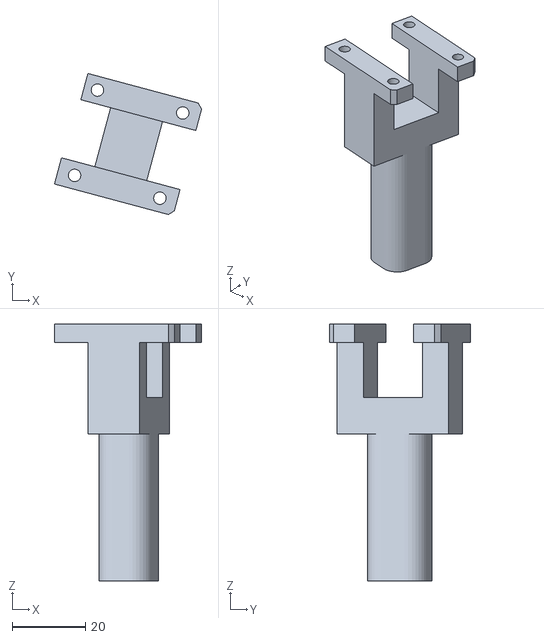
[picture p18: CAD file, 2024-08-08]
cad/motor_arm_leg.stl
40.1 x 38.4 x 70.0

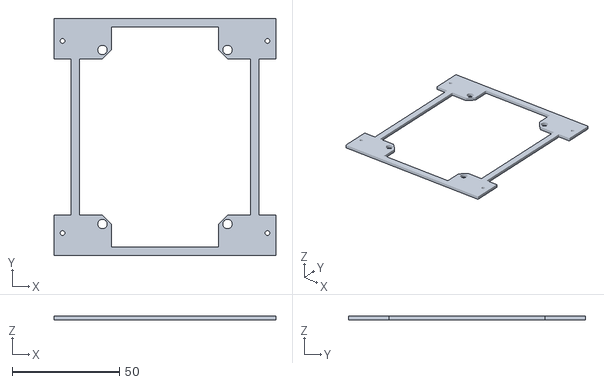
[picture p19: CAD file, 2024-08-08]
cad/case_base.stl
103.7 x 110.5 x 2.00

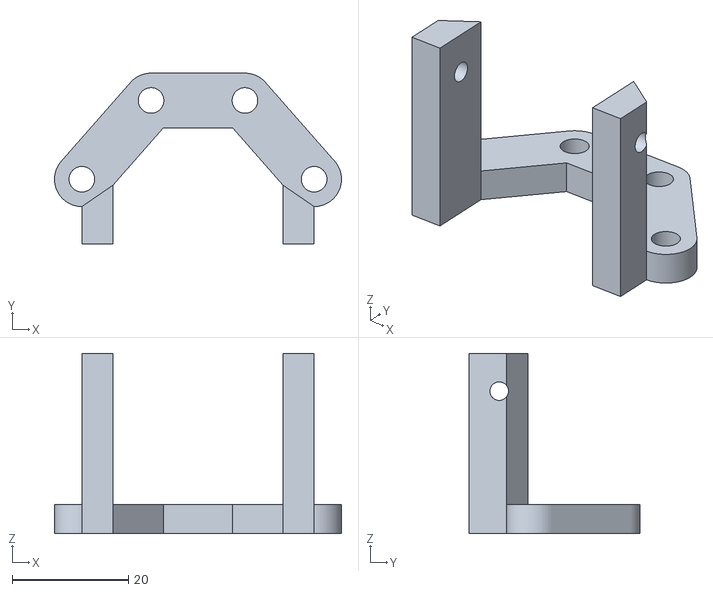
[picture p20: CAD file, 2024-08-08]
cad/camera_mount.stl
49.3 x 29.4 x 31.0

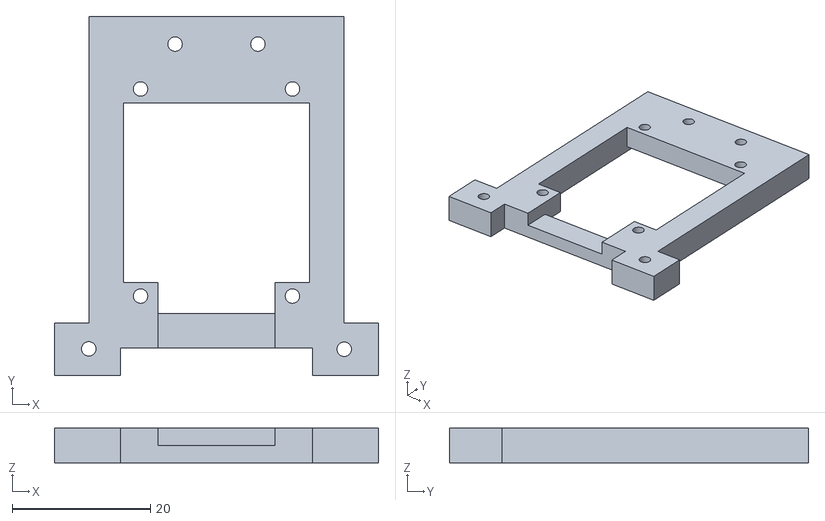
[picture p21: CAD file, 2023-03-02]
cad/gps_mount_bn357.stl
47.0 x 52.0 x 5.00

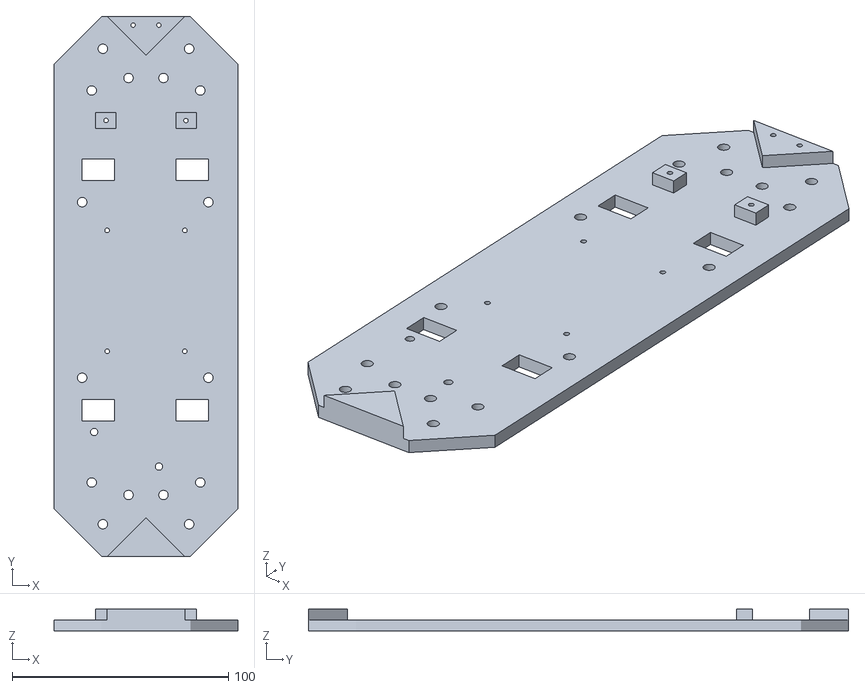
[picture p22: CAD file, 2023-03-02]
cad/body.stl
85.0 x 250.0 x 10.0

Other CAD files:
cad/failed_testing_equipment/test_arm_b.stl
cad/failed_testing_equipment/test_arm_l.stl

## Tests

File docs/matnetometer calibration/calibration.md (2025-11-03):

# How to calibrate QMC5883l

1. Disable the existing corrections for soft iron and hard iron. Like code bellow

```C
float hard_iron_correction[3] = {
    0, 0, 0
};
float soft_iron_correction[3][3] = {
    {1,0,0},
    {0,1,0},
    {0,0,1}
};
```

2. Disable axis switching for magnetometer readings

```C
// fix_mag_axis(magnetometer_data);
```

3. Print out magnetometer readings without commas at the end of every loop.

```C
printf("%6.5f %6.5f %6.5f", magnetometer_data[0], magnetometer_data[1], magnetometer_data[2]);
printf("\n"); 
```

4. Start the robot loop with usb connected. Listen to UART communication and gather it into a txt file. You have to spin the robot all around to make sure to get the maximums and minimums of each axis of the magnetometer. Example bellow with corrections already made - 

```
0.05614, 0.02117,  0.06373
0.05780, 0.02252,  0.06302
0.05780, 0.02252,  0.06302
0.05644, 0.02096,  0.06373
0.05644, 0.02096,  0.06373
0.05748, 0.02097,  0.06302
0.05748, 0.02097,  0.06302
0.05656, 0.02096,  0.06359
0.05656, 0.02096,  0.06359
0.05748, 0.02063,  0.06345
0.05748, 0.02063,  0.06345
0.05644, 0.02151,  0.06231
0.05644, 0.02151,  0.06231
```

5. Go to https://www.ngdc.noaa.gov/geomag/calculators/magcalc.shtml#igrfwmm OR https://www.magnetic-declination.com/ and find your "Norm of magnetic field". The value is going to be in nano teslas, be aware of that. We need micro teslas so divide that 50,716.7 value by 1000 and you get 50.7167. For me in Denmark it is 50.7167.

50.7234
50.7244
50.7167
50.4905
50.7167
50.7206
50.7207
50.7208
50.7226
50.7371
50.7392 

6. Open "Magneto 1.2". Point it to your txt file with magnetometer readings. Put in the Norm of magnetic field value in THE SAME UNITS as the magnetometer readings. In this case my readings are in micro tesla and the norm is in nano tesla, convert that to micro teslas also. Converting the value gives weird readings but i guess that is supposed to be the correct way. Get the calibrations from Magneto. Combined bias is hard iron calibration and the 3x3 grid bellow that is the soft iron one.
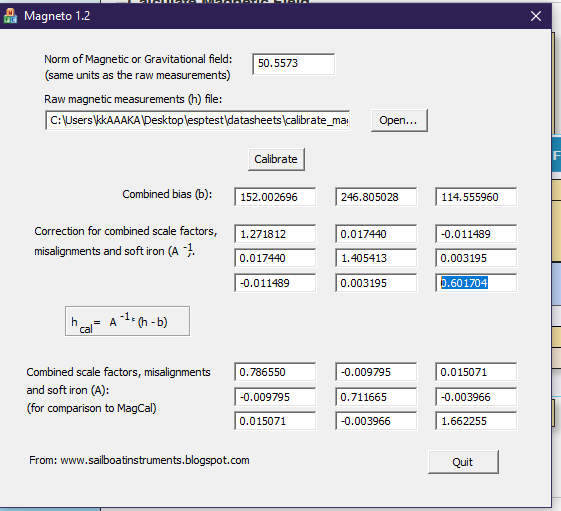
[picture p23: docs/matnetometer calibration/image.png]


7. Plug the calibrations into our calibration arrays.

```C
float hard_iron_correction[3] = {
    152.002696, 246.805028, 114.555960
};

float soft_iron_correction[3][3] = {
    {1.271812,0.017440,-0.011489},
    {0.017440,1.405413,0.003195},
    {-0.011489,0.003195,0.601704}
};
```

8. Undo the commented out axis switch.

```C
fix_mag_axis(magnetometer_data);
```

9. Compare the previous magnetometer measurements and the calibrated ones. This is how a well calibrated one looks like. I had a bad magnetometer at first so i switched mine for a new one and then it worked very good.

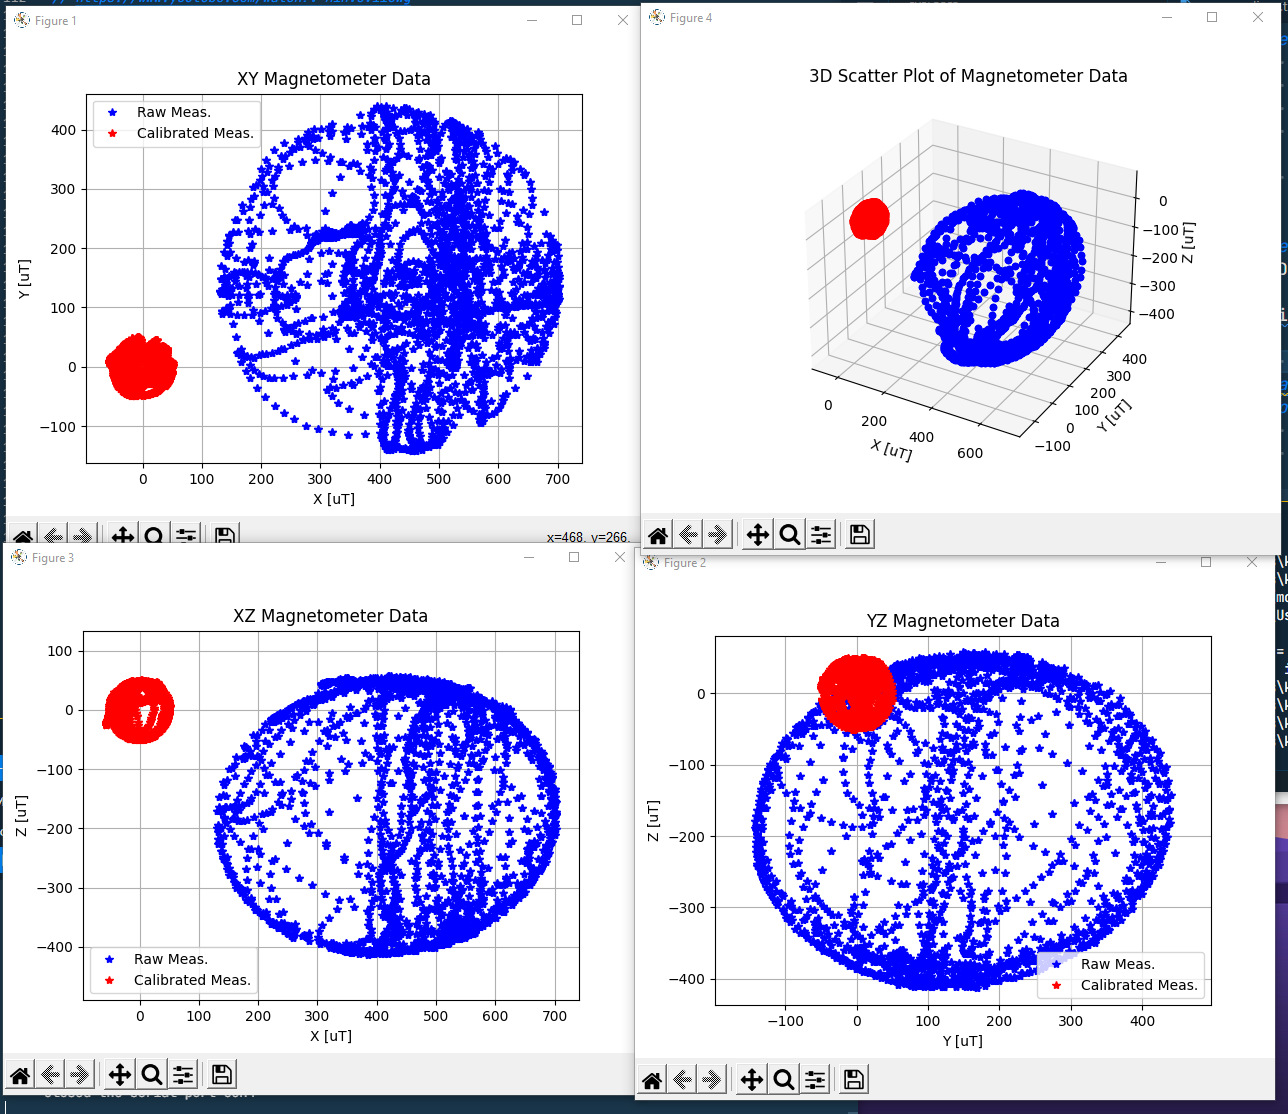
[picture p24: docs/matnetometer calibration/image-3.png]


Here is another calibration i did also very good:



# EXCEPTION SCENARIOS

### One axis is fucked in terms of range even after calibration

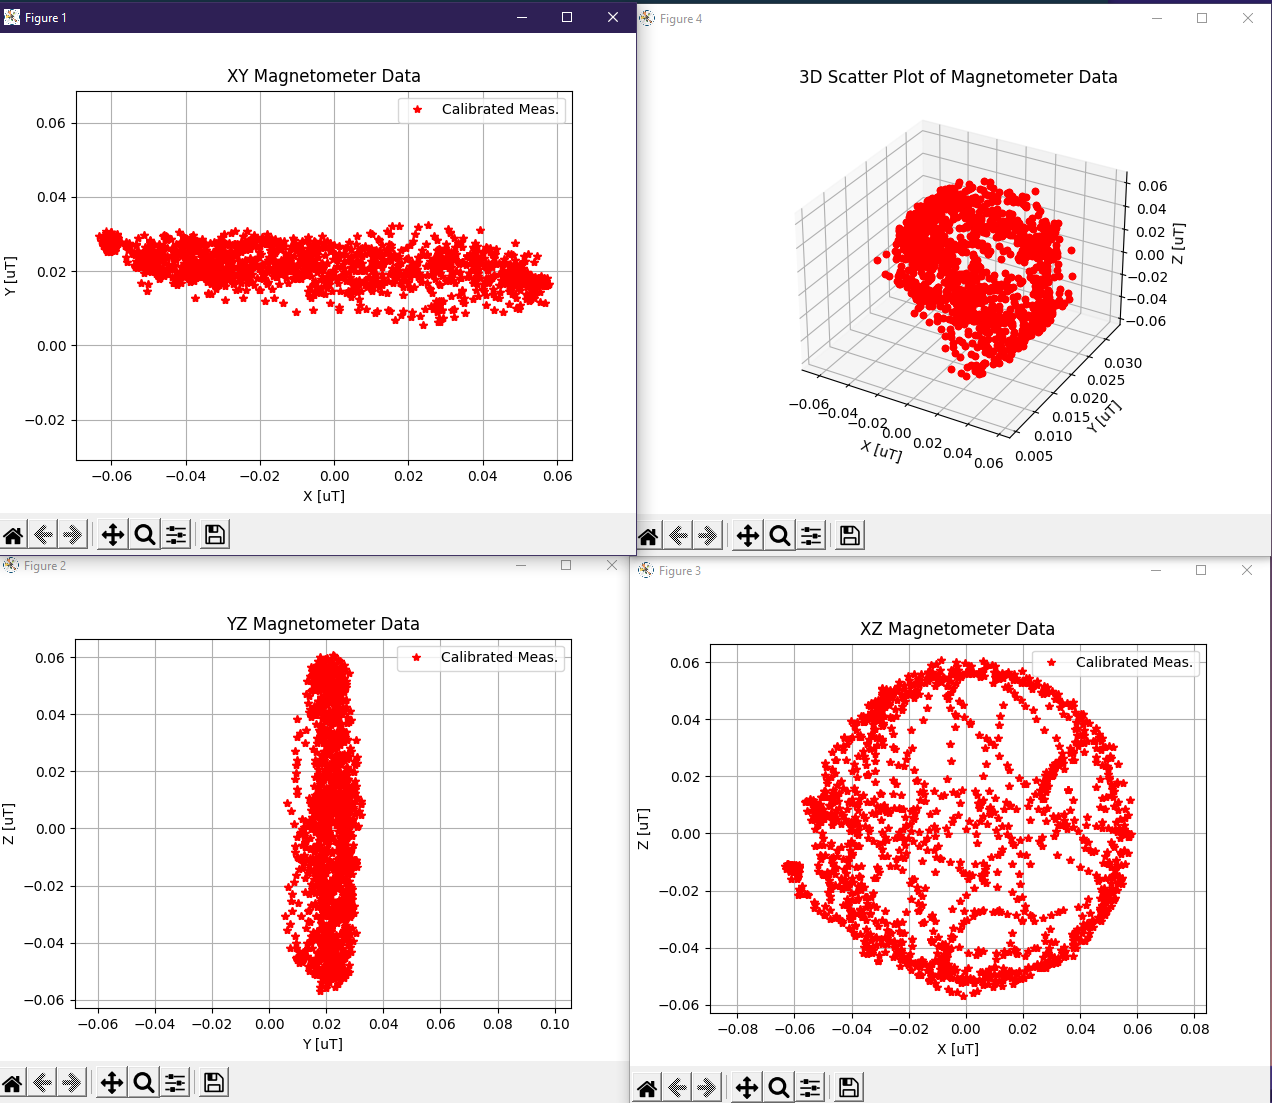
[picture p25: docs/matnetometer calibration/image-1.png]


What I tried in this case was to put a magnet next to the magnetometer, but not touch it with it. This makes it go wild but may help in getting an axis unstuck.

This is my readings from magnetometer that was calibrated before and after I put a magnet next to it. Bellow is the image. You can see the y axis was stuck before and now the x axis is stuck. At least something changed.

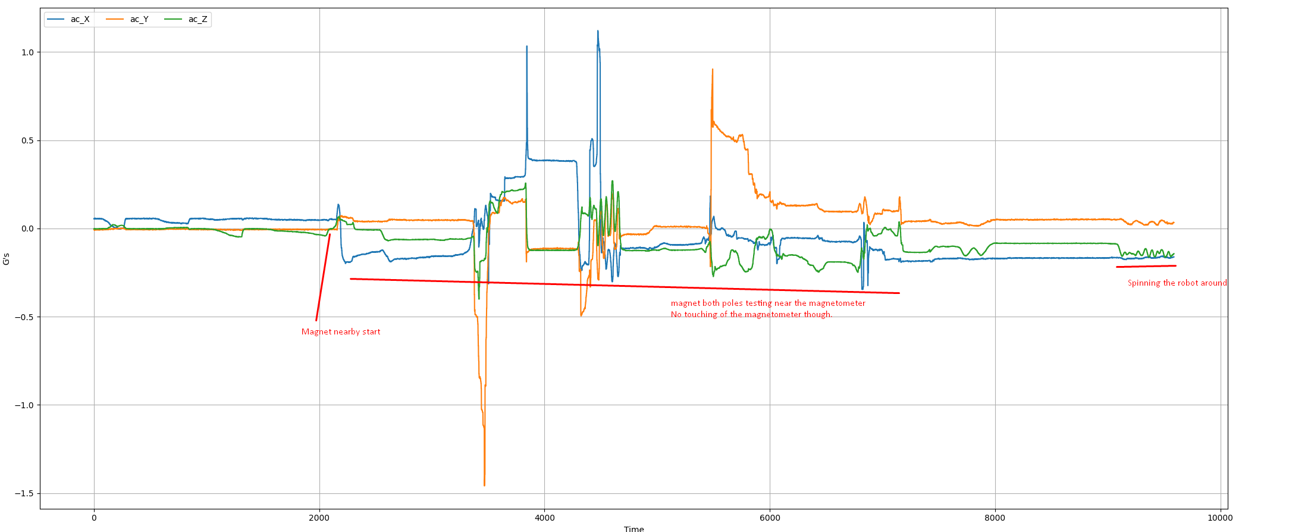
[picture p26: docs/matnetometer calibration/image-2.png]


Either you do this or just switch to a different magnetometer of the same kind.

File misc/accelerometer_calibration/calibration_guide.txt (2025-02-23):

// Accelerometer
float accelerometer_correction[3] = {
    -0.022429, -0.334548, 0.952135
};

Above numbers are not from magneto, not from, not from static error from 1000 samples either. 

I get 100 samples on level ground and then i look at the data and compare the outputs of the mpu6050 accelerometer data function
to what they are expected to be. 0.00, 0.00 and 1.00. I then adjust the correction to be that value

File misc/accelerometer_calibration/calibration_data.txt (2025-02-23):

0.022057	0.993490	0.040844
0.028785	-0.999134	0.040097
-0.954034	0.023280	-0.137805
1.016156	-0.019764	0.032705
0.086079	0.003628	-1.000183
0.179089	0.004494	-0.991115
0.105777	0.006788	-0.997536
-0.028012	-0.000809	0.958897
-0.038034	-0.010347	0.953092

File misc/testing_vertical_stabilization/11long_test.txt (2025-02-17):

0.0;0.0;0.0;0.0;0.0;0.0;0.0;0.0;0.0;0.0;0.0;0.0;
0.0;0.0;0.0;0.0;0.0;0.0;0.0;0.0;0.0;0.0;0.0;0.0;
0.0;0.0;0.0;0.0;0.0;0.0;0.0;0.0;0.0;0.0;0.0;0.0;
0.0;0.0;0.0;0.0;0.0;0.0;0.0;0.0;0.0;0.0;0.0;0.0;
0.0;0.0;0.0;0.0;0.0;0.0;0.0;0.0;0.0;0.0;0.0;0.0;
0.0;0.0;0.0;0.0;0.0;0.0;0.0;0.0;0.0;0.0;0.0;0.0;
0.0;0.0;0.0;0.0;0.0;0.0;0.0;0.0;0.0;0.0;0.0;0.0;
0.0;0.0;0.0;0.0;0.0;0.0;0.0;0.0;0.0;0.0;0.0;0.0;
0.0;0.0;0.0;0.0;0.0;0.0;0.0;0.0;0.0;0.0;0.0;0.0;
0.0;0.0;0.0;0.0;0.0;0.0;0.0;0.0;0.0;0.0;0.0;0.0;
0.0;0.0;0.0;0.0;0.0;0.0;0.0;0.0;0.0;0.0;0.0;0.0;
0.0;0.0;0.0;0.0;0.0;0.0;0.0;0.0;0.0;0.0;0.0;0.0;
0.0;0.0;0.0;0.0;0.0;0.0;0.0;0.0;0.0;0.0;0.0;0.0;
0.0;0.0;0.0;0.0;0.0;0.0;0.0;0.0;0.0;0.0;0.0;0.0;
0.0;0.0;0.0;0.0;0.0;0.0;0.0;0.0;0.0;0.0;0.0;0.0;
0.0;0.0;0.0;0.0;0.0;0.0;0.0;0.0;0.0;0.0;0.0;0.0;
0.0;0.0;0.0;0.0;0.0;0.0;0.0;0.0;0.0;0.0;0.0;0.0;
0.0;0.0;0.0;0.0;0.0;0.0;0.0;0.0;0.0;0.0;0.0;0.0;
0.0;0.0;0.0;0.0;0.0;0.0;0.0;0.0;0.0;0.0;0.0;0.0;
0.0;0.0;0.0;0.0;0.0;0.0;0.0;0.0;0.0;0.0;0.0;0.0;
0.0;0.0;0.0;0.0;0.0;0.0;0.0;0.0;0.0;0.0;0.0;0.0;
0.0;0.0;0.0;0.0;0.0;0.0;0.0;0.0;0.0;0.0;0.0;0.0;
0.0;0.0;0.0;0.0;0.0;0.0;0.0;0.0;0.0;0.0;0.0;0.0;
0.0;0.0;0.0;0.0;0.0;0.0;0.0;0.0;0.0;0.0;0.0;0.0;
0.0;0.0;0.0;0.0;0.0;0.0;0.0;0.0;0.0;0.0;0.0;0.0;
0.0;0.0;0.0;0.0;0.0;0.0;0.0;0.0;0.0;0.0;0.0;0.0;
0.0;0.0;0.0;0.0;0.0;0.0;0.0;0.0;0.0;0.0;0.0;0.0;
0.0;0.0;0.0;0.0;0.0;0.0;0.0;0.0;0.0;0.0;0.0;0.0;
0.0;0.0;0.0;0.0;0.0;0.0;0.0;0.0;0.0;0.0;0.0;0.0;
0.0;0.0;0.0;0.0;0.0;0.0;0.0;0.0;0.0;0.0;0.0;0.0;
0.0;0.0;0.0;0.0;0.0;0.0;0.0;0.0;0.0;0.0;0.0;0.0;
0.0;0.0;0.0;0.0;0.0;0.0;0.0;0.0;0.0;0.0;0.0;0.0;
0.0;0.0;0.0;0.0;0.0;0.0;0.0;0.0;0.0;0.0;0.0;0.0;
0.0;0.0;0.0;0.0;0.0;0.0;0.0;0.0;0.0;0.0;0.0;0.0;
0.0;0.0;0.0;0.0;0.0;0.0;0.0;0.0;0.0;0.0;0.0;0.0;
0.0;0.0;0.0;0.0;0.0;0.0;0.0;0.0;0.0;0.0;0.0;0.0;
0.0;0.0;0.0;0.0;0.0;0.0;0.0;0.0;0.0;0.0;0.0;0.0;
0.0;0.0;0.0;0.0;0.0;0.0;0.0;0.0;0.0;0.0;0.0;0.0;
0.0;0.0;0.0;0.0;0.0;0.0;0.0;0.0;0.0;0.0;0.0;0.0;
0.0;0.0;0.0;0.0;0.0;0.0;0.0;0.0;0.0;0.0;0.0;0.0;
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

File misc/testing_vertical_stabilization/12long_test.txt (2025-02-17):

0.0;0.0;0.0;0.0;0.0;0.0;0.0;0.0;0.0;0.0;0.0;0.0;
0.0;0.0;0.0;0.0;0.0;0.0;0.0;0.0;0.0;0.0;0.0;0.0;
0.0;0.0;0.0;0.0;0.0;0.0;0.0;0.0;0.0;0.0;0.0;0.0;
0.0;0.0;0.0;0.0;0.0;0.0;0.0;0.0;0.0;0.0;0.0;0.0;
0.0;0.0;0.0;0.0;0.0;0.0;0.0;0.0;0.0;0.0;0.0;0.0;
0.0;0.0;0.0;0.0;0.0;0.0;0.0;0.0;0.0;0.0;0.0;0.0;
0.0;0.0;0.0;0.0;0.0;0.0;0.0;0.0;0.0;0.0;0.0;0.0;
0.0;0.0;0.0;0.0;0.0;0.0;0.0;0.0;0.0;0.0;0.0;0.0;
0.0;0.0;0.0;0.0;0.0;0.0;0.0;0.0;0.0;0.0;0.0;0.0;
0.0;0.0;0.0;0.0;0.0;0.0;0.0;0.0;0.0;0.0;0.0;0.0;
0.0;0.0;0.0;0.0;0.0;0.0;0.0;0.0;0.0;0.0;0.0;0.0;
0.0;0.0;0.0;0.0;0.0;0.0;0.0;0.0;0.0;0.0;0.0;0.0;
0.0;0.0;0.0;0.0;0.0;0.0;0.0;0.0;0.0;0.0;0.0;0.0;
0.0;0.0;0.0;0.0;0.0;0.0;0.0;0.0;0.0;0.0;0.0;0.0;
0.0;0.0;0.0;0.0;0.0;0.0;0.0;0.0;0.0;0.0;0.0;0.0;
0.0;0.0;0.0;0.0;0.0;0.0;0.0;0.0;0.0;0.0;0.0;0.0;
0.0;0.0;0.0;0.0;0.0;0.0;0.0;0.0;0.0;0.0;0.0;0.0;
0.0;0.0;0.0;0.0;0.0;0.0;0.0;0.0;0.0;0.0;0.0;0.0;
0.0;0.0;0.0;0.0;0.0;0.0;0.0;0.0;0.0;0.0;0.0;0.0;
0.0;0.0;0.0;0.0;0.0;0.0;0.0;0.0;0.0;0.0;0.0;0.0;
0.0;0.0;0.0;0.0;0.0;0.0;0.0;0.0;0.0;0.0;0.0;0.0;
0.0;0.0;0.0;0.0;0.0;0.0;0.0;0.0;0.0;0.0;0.0;0.0;
0.0;0.0;0.0;0.0;0.0;0.0;0.0;0.0;0.0;0.0;0.0;0.0;
0.0;0.0;0.0;0.0;0.0;0.0;0.0;0.0;0.0;0.0;0.0;0.0;
0.0;0.0;0.0;0.0;0.0;0.0;0.0;0.0;0.0;0.0;0.0;0.0;
0.0;0.0;0.0;0.0;0.0;0.0;0.0;0.0;0.0;0.0;0.0;0.0;
0.0;0.0;0.0;0.0;0.0;0.0;0.0;0.0;0.0;0.0;0.0;0.0;
0.0;0.0;0.0;0.0;0.0;0.0;0.0;0.0;0.0;0.0;0.0;0.0;
0.0;0.0;0.0;0.0;0.0;0.0;0.0;0.0;0.0;0.0;0.0;0.0;
0.0;0.0;0.0;0.0;0.0;0.0;0.0;0.0;0.0;0.0;0.0;0.0;
0.0;0.0;0.0;0.0;0.0;0.0;0.0;0.0;0.0;0.0;0.0;0.0;
0.0;0.0;0.0;0.0;0.0;0.0;0.0;0.0;0.0;0.0;0.0;0.0;
0.0;0.0;0.0;0.0;0.0;0.0;0.0;0.0;0.0;0.0;0.0;0.0;
0.0;0.0;0.0;0.0;0.0;0.0;0.0;0.0;0.0;0.0;0.0;0.0;
0.0;0.0;0.0;0.0;0.0;0.0;0.0;0.0;0.0;0.0;0.0;0.0;
0.0;0.0;0.0;0.0;0.0;0.0;0.0;0.0;0.0;0.0;0.0;0.0;
0.0;0.0;0.0;0.0;0.0;0.0;0.0;0.0;0.0;0.0;0.0;0.0;
0.0;0.0;0.0;0.0;0.0;0.0;0.0;0.0;0.0;0.0;0.0;0.0;
0.0;0.0;0.0;0.0;0.0;0.0;0.0;0.0;0.0;0.0;0.0;0.0;
0.0;0.0;0.0;0.0;0.0;0.0;0.0;0.0;0.0;0.0;0.0;0.0;
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

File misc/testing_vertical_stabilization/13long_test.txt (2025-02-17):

0.0;0.0;0.0;0.0;0.0;0.0;0.0;0.0;0.0;0.0;0.0;0.0;
0.0;0.0;0.0;0.0;0.0;0.0;0.0;0.0;0.0;0.0;0.0;0.0;
0.0;0.0;0.0;0.0;0.0;0.0;0.0;0.0;0.0;0.0;0.0;0.0;
0.0;0.0;0.0;0.0;0.0;0.0;0.0;0.0;0.0;0.0;0.0;0.0;
0.0;0.0;0.0;0.0;0.0;0.0;0.0;0.0;0.0;0.0;0.0;0.0;
0.0;0.0;0.0;0.0;0.0;0.0;0.0;0.0;0.0;0.0;0.0;0.0;
0.0;0.0;0.0;0.0;0.0;0.0;0.0;0.0;0.0;0.0;0.0;0.0;
0.0;0.0;0.0;0.0;0.0;0.0;0.0;0.0;0.0;0.0;0.0;0.0;
0.0;0.0;0.0;0.0;0.0;0.0;0.0;0.0;0.0;0.0;0.0;0.0;
0.0;0.0;0.0;0.0;0.0;0.0;0.0;0.0;0.0;0.0;0.0;0.0;
0.0;0.0;0.0;0.0;0.0;0.0;0.0;0.0;0.0;0.0;0.0;0.0;
0.0;0.0;0.0;0.0;0.0;0.0;0.0;0.0;0.0;0.0;0.0;0.0;
0.0;0.0;0.0;0.0;0.0;0.0;0.0;0.0;0.0;0.0;0.0;0.0;
0.0;0.0;0.0;0.0;0.0;0.0;0.0;0.0;0.0;0.0;0.0;0.0;
0.0;0.0;0.0;0.0;0.0;0.0;0.0;0.0;0.0;0.0;0.0;0.0;
0.0;0.0;0.0;0.0;0.0;0.0;0.0;0.0;0.0;0.0;0.0;0.0;
0.0;0.0;0.0;0.0;0.0;0.0;0.0;0.0;0.0;0.0;0.0;0.0;
0.0;0.0;0.0;0.0;0.0;0.0;0.0;0.0;0.0;0.0;0.0;0.0;
0.0;0.0;0.0;0.0;0.0;0.0;0.0;0.0;0.0;0.0;0.0;0.0;
0.0;0.0;0.0;0.0;0.0;0.0;0.0;0.0;0.0;0.0;0.0;0.0;
0.0;0.0;0.0;0.0;0.0;0.0;0.0;0.0;0.0;0.0;0.0;0.0;
0.0;0.0;0.0;0.0;0.0;0.0;0.0;0.0;0.0;0.0;0.0;0.0;
0.0;0.0;0.0;0.0;0.0;0.0;0.0;0.0;0.0;0.0;0.0;0.0;
0.0;0.0;0.0;0.0;0.0;0.0;0.0;0.0;0.0;0.0;0.0;0.0;
0.0;0.0;0.0;0.0;0.0;0.0;0.0;0.0;0.0;0.0;0.0;0.0;
0.0;0.0;0.0;0.0;0.0;0.0;0.0;0.0;0.0;0.0;0.0;0.0;
0.0;0.0;0.0;0.0;0.0;0.0;0.0;0.0;0.0;0.0;0.0;0.0;
0.0;0.0;0.0;0.0;0.0;0.0;0.0;0.0;0.0;0.0;0.0;0.0;
0.0;0.0;0.0;0.0;0.0;0.0;0.0;0.0;0.0;0.0;0.0;0.0;
0.0;0.0;0.0;0.0;0.0;0.0;0.0;0.0;0.0;0.0;0.0;0.0;
0.0;0.0;0.0;0.0;0.0;0.0;0.0;0.0;0.0;0.0;0.0;0.0;
0.0;0.0;0.0;0.0;0.0;0.0;0.0;0.0;0.0;0.0;0.0;0.0;
0.0;0.0;0.0;0.0;0.0;0.0;0.0;0.0;0.0;0.0;0.0;0.0;
0.0;0.0;0.0;0.0;0.0;0.0;0.0;0.0;0.0;0.0;0.0;0.0;
0.0;0.0;0.0;0.0;0.0;0.0;0.0;0.0;0.0;0.0;0.0;0.0;
0.0;0.0;0.0;0.0;0.0;0.0;0.0;0.0;0.0;0.0;0.0;0.0;
0.0;0.0;0.0;0.0;0.0;0.0;0.0;0.0;0.0;0.0;0.0;0.0;
0.0;0.0;0.0;0.0;0.0;0.0;0.0;0.0;0.0;0.0;0.0;0.0;
0.0;0.0;0.0;0.0;0.0;0.0;0.0;0.0;0.0;0.0;0.0;0.0;
0.0;0.0;0.0;0.0;0.0;0.0;0.0;0.0;0.0;0.0;0.0;0.0;
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

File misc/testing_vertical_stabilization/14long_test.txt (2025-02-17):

0.0;0.0;0.0;0.0;0.0;0.0;0.0;0.0;0.0;0.0;0.0;0.0;
0.0;0.0;0.0;0.0;0.0;0.0;0.0;0.0;0.0;0.0;0.0;0.0;
0.0;0.0;0.0;0.0;0.0;0.0;0.0;0.0;0.0;0.0;0.0;0.0;
0.0;0.0;0.0;0.0;0.0;0.0;0.0;0.0;0.0;0.0;0.0;0.0;
0.0;0.0;0.0;0.0;0.0;0.0;0.0;0.0;0.0;0.0;0.0;0.0;
0.0;0.0;0.0;0.0;0.0;0.0;0.0;0.0;0.0;0.0;0.0;0.0;
0.0;0.0;0.0;0.0;0.0;0.0;0.0;0.0;0.0;0.0;0.0;0.0;
0.0;0.0;0.0;0.0;0.0;0.0;0.0;0.0;0.0;0.0;0.0;0.0;
0.0;0.0;0.0;0.0;0.0;0.0;0.0;0.0;0.0;0.0;0.0;0.0;
0.0;0.0;0.0;0.0;0.0;0.0;0.0;0.0;0.0;0.0;0.0;0.0;
0.0;0.0;0.0;0.0;0.0;0.0;0.0;0.0;0.0;0.0;0.0;0.0;
0.0;0.0;0.0;0.0;0.0;0.0;0.0;0.0;0.0;0.0;0.0;0.0;
0.0;0.0;0.0;0.0;0.0;0.0;0.0;0.0;0.0;0.0;0.0;0.0;
0.0;0.0;0.0;0.0;0.0;0.0;0.0;0.0;0.0;0.0;0.0;0.0;
0.0;0.0;0.0;0.0;0.0;0.0;0.0;0.0;0.0;0.0;0.0;0.0;
0.0;0.0;0.0;0.0;0.0;0.0;0.0;0.0;0.0;0.0;0.0;0.0;
0.0;0.0;0.0;0.0;0.0;0.0;0.0;0.0;0.0;0.0;0.0;0.0;
0.0;0.0;0.0;0.0;0.0;0.0;0.0;0.0;0.0;0.0;0.0;0.0;
0.0;0.0;0.0;0.0;0.0;0.0;0.0;0.0;0.0;0.0;0.0;0.0;
0.0;0.0;0.0;0.0;0.0;0.0;0.0;0.0;0.0;0.0;0.0;0.0;
0.0;0.0;0.0;0.0;0.0;0.0;0.0;0.0;0.0;0.0;0.0;0.0;
0.0;0.0;0.0;0.0;0.0;0.0;0.0;0.0;0.0;0.0;0.0;0.0;
0.0;0.0;0.0;0.0;0.0;0.0;0.0;0.0;0.0;0.0;0.0;0.0;
0.0;0.0;0.0;0.0;0.0;0.0;0.0;0.0;0.0;0.0;0.0;0.0;
0.0;0.0;0.0;0.0;0.0;0.0;0.0;0.0;0.0;0.0;0.0;0.0;
0.0;0.0;0.0;0.0;0.0;0.0;0.0;0.0;0.0;0.0;0.0;0.0;
0.0;0.0;0.0;0.0;0.0;0.0;0.0;0.0;0.0;0.0;0.0;0.0;
0.0;0.0;0.0;0.0;0.0;0.0;0.0;0.0;0.0;0.0;0.0;0.0;
0.0;0.0;0.0;0.0;0.0;0.0;0.0;0.0;0.0;0.0;0.0;0.0;
0.0;0.0;0.0;0.0;0.0;0.0;0.0;0.0;0.0;0.0;0.0;0.0;
0.0;0.0;0.0;0.0;0.0;0.0;0.0;0.0;0.0;0.0;0.0;0.0;
0.0;0.0;0.0;0.0;0.0;0.0;0.0;0.0;0.0;0.0;0.0;0.0;
0.0;0.0;0.0;0.0;0.0;0.0;0.0;0.0;0.0;0.0;0.0;0.0;
0.0;0.0;0.0;0.0;0.0;0.0;0.0;0.0;0.0;0.0;0.0;0.0;
0.0;0.0;0.0;0.0;0.0;0.0;0.0;0.0;0.0;0.0;0.0;0.0;
0.0;0.0;0.0;0.0;0.0;0.0;0.0;0.0;0.0;0.0;0.0;0.0;
0.0;0.0;0.0;0.0;0.0;0.0;0.0;0.0;0.0;0.0;0.0;0.0;
0.0;0.0;0.0;0.0;0.0;0.0;0.0;0.0;0.0;0.0;0.0;0.0;
0.0;0.0;0.0;0.0;0.0;0.0;0.0;0.0;0.0;0.0;0.0;0.0;
0.0;0.0;0.0;0.0;0.0;0.0;0.0;0.0;0.0;0.0;0.0;0.0;
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

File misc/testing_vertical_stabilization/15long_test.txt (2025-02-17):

0.0;0.0;0.0;0.0;0.0;0.0;0.0;0.0;0.0;0.0;0.0;0.0;
0.0;0.0;0.0;0.0;0.0;0.0;0.0;0.0;0.0;0.0;0.0;0.0;
0.0;0.0;0.0;0.0;0.0;0.0;0.0;0.0;0.0;0.0;0.0;0.0;
0.0;0.0;0.0;0.0;0.0;0.0;0.0;0.0;0.0;0.0;0.0;0.0;
0.0;0.0;0.0;0.0;0.0;0.0;0.0;0.0;0.0;0.0;0.0;0.0;
0.0;0.0;0.0;0.0;0.0;0.0;0.0;0.0;0.0;0.0;0.0;0.0;
0.0;0.0;0.0;0.0;0.0;0.0;0.0;0.0;0.0;0.0;0.0;0.0;
0.0;0.0;0.0;0.0;0.0;0.0;0.0;0.0;0.0;0.0;0.0;0.0;
0.0;0.0;0.0;0.0;0.0;0.0;0.0;0.0;0.0;0.0;0.0;0.0;
0.0;0.0;0.0;0.0;0.0;0.0;0.0;0.0;0.0;0.0;0.0;0.0;
0.0;0.0;0.0;0.0;0.0;0.0;0.0;0.0;0.0;0.0;0.0;0.0;
0.0;0.0;0.0;0.0;0.0;0.0;0.0;0.0;0.0;0.0;0.0;0.0;
0.0;0.0;0.0;0.0;0.0;0.0;0.0;0.0;0.0;0.0;0.0;0.0;
0.0;0.0;0.0;0.0;0.0;0.0;0.0;0.0;0.0;0.0;0.0;0.0;
0.0;0.0;0.0;0.0;0.0;0.0;0.0;0.0;0.0;0.0;0.0;0.0;
0.0;0.0;0.0;0.0;0.0;0.0;0.0;0.0;0.0;0.0;0.0;0.0;
0.0;0.0;0.0;0.0;0.0;0.0;0.0;0.0;0.0;0.0;0.0;0.0;
0.0;0.0;0.0;0.0;0.0;0.0;0.0;0.0;0.0;0.0;0.0;0.0;
0.0;0.0;0.0;0.0;0.0;0.0;0.0;0.0;0.0;0.0;0.0;0.0;
0.0;0.0;0.0;0.0;0.0;0.0;0.0;0.0;0.0;0.0;0.0;0.0;
0.0;0.0;0.0;0.0;0.0;0.0;0.0;0.0;0.0;0.0;0.0;0.0;
0.0;0.0;0.0;0.0;0.0;0.0;0.0;0.0;0.0;0.0;0.0;0.0;
0.0;0.0;0.0;0.0;0.0;0.0;0.0;0.0;0.0;0.0;0.0;0.0;
0.0;0.0;0.0;0.0;0.0;0.0;0.0;0.0;0.0;0.0;0.0;0.0;
0.0;0.0;0.0;0.0;0.0;0.0;0.0;0.0;0.0;0.0;0.0;0.0;
0.0;0.0;0.0;0.0;0.0;0.0;0.0;0.0;0.0;0.0;0.0;0.0;
0.0;0.0;0.0;0.0;0.0;0.0;0.0;0.0;0.0;0.0;0.0;0.0;
0.0;0.0;0.0;0.0;0.0;0.0;0.0;0.0;0.0;0.0;0.0;0.0;
0.0;0.0;0.0;0.0;0.0;0.0;0.0;0.0;0.0;0.0;0.0;0.0;
0.0;0.0;0.0;0.0;0.0;0.0;0.0;0.0;0.0;0.0;0.0;0.0;
0.0;0.0;0.0;0.0;0.0;0.0;0.0;0.0;0.0;0.0;0.0;0.0;
0.0;0.0;0.0;0.0;0.0;0.0;0.0;0.0;0.0;0.0;0.0;0.0;
0.0;0.0;0.0;0.0;0.0;0.0;0.0;0.0;0.0;0.0;0.0;0.0;
0.0;0.0;0.0;0.0;0.0;0.0;0.0;0.0;0.0;0.0;0.0;0.0;
0.0;0.0;0.0;0.0;0.0;0.0;0.0;0.0;0.0;0.0;0.0;0.0;
0.0;0.0;0.0;0.0;0.0;0.0;0.0;0.0;0.0;0.0;0.0;0.0;
0.0;0.0;0.0;0.0;0.0;0.0;0.0;0.0;0.0;0.0;0.0;0.0;
0.0;0.0;0.0;0.0;0.0;0.0;0.0;0.0;0.0;0.0;0.0;0.0;
0.0;0.0;0.0;0.0;0.0;0.0;0.0;0.0;0.0;0.0;0.0;0.0;
0.0;0.0;0.0;0.0;0.0;0.0;0.0;0.0;0.0;0.0;0.0;0.0;
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

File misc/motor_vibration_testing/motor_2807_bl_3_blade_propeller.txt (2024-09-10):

0.043701;-0.010099;1.021819;0.005741;0.261102;0.127191;
0.047336;-0.029717;1.035563;0.051542;0.108430;-0.262122;
0.057729;-0.000744;1.031717;0.196580;0.009193;-0.170519;
0.029948;0.031776;1.030079;0.013374;0.352705;0.005053;
0.033280;0.041626;1.042530;0.028641;0.054995;0.035588;
0.026138;0.043347;1.050546;-0.040061;0.276369;0.096657;
0.024285;0.000542;1.030280;0.097344;0.062629;0.027954;
0.039839;-0.014648;1.023659;0.303450;0.032094;0.081389;
0.061981;-0.005103;1.036373;0.127878;-0.097677;-0.353725;
0.026183;0.022196;1.020813;0.005741;0.306903;-0.132351;
0.042342;0.044610;1.033138;-0.085862;-0.112944;-0.002580;
0.032697;0.048956;1.045571;-0.062962;0.039728;0.134824;
0.015364;0.008619;1.028554;-0.017160;0.001560;0.188260;
0.065186;-0.019582;1.035963;0.196580;0.077896;0.058489;
0.047386;0.006598;1.017699;0.112611;-0.082409;-0.139985;
0.025810;0.010886;1.015494;-0.040061;0.261102;-0.124718;
0.034743;0.041690;1.042061;-0.208000;0.268735;0.073756;
0.019127;0.040054;1.031762;-0.154565;0.093163;0.119557;
0.009962;0.024853;1.022828;-0.001893;0.062629;0.081389;
0.044519;-0.025094;1.027498;0.135512;0.123697;-0.071282;
0.055448;-0.003018;1.033859;-0.032427;-0.006073;-0.361359;
0.026229;0.032942;1.021950;0.104977;0.154232;-0.056015;
0.031640;0.042994;1.024625;-0.230901;-0.044241;0.027954;
0.030898;0.048087;1.042100;-0.246168;0.085529;0.035588;
0.025221;0.002859;1.018802;-0.017160;-0.204547;0.195893;
0.070629;-0.017180;1.032152;0.127878;-0.067142;-0.056015;
0.037158;0.008020;1.015368;0.143145;0.123697;-0.262122;
0.028009;0.018439;1.024708;0.127878;0.352705;-0.086550;
0.042624;0.044430;1.036573;0.089710;0.238201;0.104290;
0.013940;0.033716;1.032332;-0.124030;-0.021341;0.157725;
0.020638;0.016671;1.028256;0.204214;0.116064;0.142458;
0.055142;-0.024026;1.032078;0.028641;0.146598;-0.056015;
0.050047;0.002271;1.013015;0.211847;-0.112944;-0.056015;
0.033571;0.008863;1.018272;0.051542;0.360339;0.089023;
0.032088;0.039730;1.033412;0.051542;0.238201;0.027954;
0.028859;0.044181;1.031715;0.005741;0.085529;0.089023;
0.012093;0.028607;1.022422;-0.162198;-0.028975;0.264595;
0.050160;-0.019465;1.026924;0.104977;0.108430;0.005053;
0.058353;-0.003145;1.032182;0.104977;0.039728;-0.162885;
0.046413;0.003777;1.028189;0.127878;0.406140;-0.155252;
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

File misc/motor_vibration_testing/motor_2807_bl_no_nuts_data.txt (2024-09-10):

0.059975;0.023136;1.040188;-0.075374;0.034024;-0.232588;
0.043247;0.029672;1.008657;-0.083007;-0.065212;-0.118084;
0.018442;0.029124;1.020068;0.184168;-0.233151;0.026954;
0.013053;0.037012;1.027217;0.031496;0.011124;0.103290;
0.060146;0.001656;1.020997;0.214703;0.056925;-0.110451;
0.075961;0.008140;1.028672;-0.304381;0.034024;-0.110451;
0.036299;0.014841;1.017907;0.046764;0.056925;0.004053;
0.013907;0.026229;1.020452;0.000962;-0.202617;0.179626;
0.022676;0.038262;1.047725;0.245237;-0.340021;0.294130;
0.020474;0.020685;1.019729;0.176535;0.095093;0.049855;
0.072387;0.006428;1.023447;-0.197511;0.179062;-0.049382;
0.019411;0.021707;1.009675;-0.220412;0.087460;-0.026481;
-0.001042;0.020847;1.018690;-0.090641;-0.309487;0.194893;
0.014305;0.043626;1.042044;-0.052473;-0.217884;0.103290;
0.017627;0.011799;1.021766;0.031496;-0.042312;0.042221;
0.069691;0.001432;1.040992;-0.250946;0.072192;-0.087550;
0.033695;0.013418;1.029375;-0.067740;-0.126281;0.072756;
0.010456;0.014879;1.022690;0.031496;-0.111014;0.034588;
0.025625;0.043067;1.049799;0.039130;0.232498;0.057488;
0.040990;0.017441;1.030272;0.130733;0.003490;0.072756;
0.062879;0.002290;1.022026;-0.250946;0.011124;-0.034115;
0.069672;0.018402;1.051292;-0.205145;0.133261;-0.148618;
0.018983;0.020128;1.019945;0.069664;0.247765;0.065122;
0.032266;0.046658;1.039891;-0.083007;-0.210250;0.271229;
0.018002;0.033363;1.044890;0.176535;-0.080480;-0.026481;
0.067434;0.001250;1.019132;-0.289114;0.171429;-0.140985;
0.074226;0.023153;1.027394;-0.006671;0.064559;-0.247855;
0.011884;0.022571;1.010316;-0.052473;-0.065212;0.034588;
0.022936;0.037808;1.032274;0.054397;-0.072846;0.271229;
0.014377;0.028567;1.028830;-0.067740;-0.126281;0.095656;
0.062463;-0.004180;1.014324;0.168901;0.415704;-0.140985;
0.067399;0.012855;1.029355;0.008596;0.018757;-0.240222;
0.023859;0.015223;1.018471;0.275771;0.148528;0.072756;
0.026883;0.023835;1.030655;0.062031;-0.172082;0.156725;
0.016958;0.027416;1.024926;0.222336;0.171429;0.065122;
0.063528;0.000149;1.023475;0.245237;0.331734;0.072756;
0.079989;-0.003893;1.026102;0.000962;0.270666;-0.224954;
0.039258;0.014077;1.022597;-0.067740;-0.042312;-0.194420;
0.023686;0.029016;1.028723;-0.037206;-0.034678;0.126191;
0.010571;0.034079;1.034986;0.146000;-0.149182;0.240694;
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

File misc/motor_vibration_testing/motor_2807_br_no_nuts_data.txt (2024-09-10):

0.037047;0.028600;1.005856;-0.051366;0.098572;-0.017695;
0.081114;0.026797;1.054029;-0.379611;-0.008298;-0.032962;
0.007638;0.008323;1.000240;0.147107;0.129106;-0.055863;
0.006284;0.014902;1.021405;0.253977;-0.023565;-0.231435;
0.030961;0.031646;1.051425;0.200542;-0.260207;-0.055863;
0.056902;0.036560;1.017779;-0.326175;0.060404;0.203679;
0.080351;0.022773;1.048074;-0.341443;0.098572;0.073908;
0.041340;0.012681;1.037074;-0.104801;-0.183871;-0.223802;
0.020643;0.016193;1.012064;0.170008;-0.099901;-0.086397;
0.026025;0.024613;1.036785;0.024970;-0.451046;-0.025328;
0.058838;0.041050;1.018362;-0.135336;-0.038833;0.089176;
0.071011;0.018332;1.041992;0.024970;0.014602;0.066275;
0.028917;0.002827;1.021061;0.162374;0.037503;0.081542;
0.025997;0.025028;1.014966;0.337947;-0.000665;-0.101664;
0.022107;0.024889;1.035262;0.162374;-0.191504;-0.155099;
0.068243;0.038108;1.019434;-0.257473;0.022236;0.150244;
0.097205;0.038192;1.046330;-0.272740;0.167274;-0.010061;
0.021843;0.008310;1.002403;0.246344;0.113839;-0.063496;
0.025666;0.034480;1.029076;0.307412;-0.046466;-0.116931;
0.015953;0.031319;1.045322;0.177641;-0.130436;-0.200901;
0.075834;0.044302;1.034590;-0.051366;0.152007;0.012840;
0.091367;0.040983;1.056587;-0.272740;0.297045;0.134977;
0.019421;0.004514;1.017762;-0.013198;0.182541;-0.071130;
0.030755;0.030016;1.023689;0.170008;-0.313642;-0.147466;
0.018882;0.026082;1.027386;0.200542;-0.107535;-0.032962;
0.032149;0.032091;1.010742;-0.379611;-0.092268;0.051008;
0.096713;0.027237;1.049107;-0.257473;0.228343;0.073908;
0.011968;-0.003405;1.000867;0.269244;-0.015932;0.028107;
0.034544;0.031243;1.028420;0.101306;-0.252573;-0.010061;
0.018003;0.031241;1.016169;0.093672;-0.374711;-0.101664;
0.094742;0.041535;1.032857;-0.303275;-0.008298;0.005206;
0.087312;0.037385;1.040538;-0.280374;0.235977;0.012840;
0.005986;0.001782;0.991784;0.276878;-0.115169;-0.048229;
0.028268;0.030108;1.038368;0.383748;-0.206772;-0.071130;
0.020871;0.032483;1.025056;0.170008;0.014602;-0.155099;
0.038500;0.033074;1.006923;-0.158237;0.121473;0.180779;
0.083320;0.029222;1.045758;-0.158237;0.304679;0.058641;
0.010161;0.007361;1.009580;0.246344;0.029870;-0.078763;
0.011195;0.012815;1.012371;0.246344;0.121473;0.005206;
0.031087;0.030140;1.047972;0.223443;-0.290741;0.043374;
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

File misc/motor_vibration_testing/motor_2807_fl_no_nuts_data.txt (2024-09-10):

0.042823;0.005313;1.028406;-0.109534;0.246809;0.084321;
0.040170;0.049173;1.018706;0.004969;-0.035634;0.038519;
0.063830;0.012095;1.039347;-0.132435;0.071237;-0.030183;
0.029037;0.030644;1.039122;0.142374;-0.050900;0.336229;
0.065502;0.014682;1.027147;-0.369076;-0.310443;-0.511099;
0.029201;0.009156;1.019440;0.157641;0.033069;0.374397;
0.056614;0.026269;1.015173;-0.170603;0.010168;-0.411863;
0.030778;-0.001373;1.010972;0.142374;0.025435;0.313328;
0.048542;0.041705;1.013812;-0.079000;0.048336;-0.198122;
0.042960;-0.002707;1.012842;0.004969;0.162840;0.214092;
0.044629;0.045036;1.038082;0.195809;-0.012733;0.320962;
0.065591;0.020588;1.030667;-0.208771;0.277344;-0.304992;
0.031036;0.021937;1.037308;0.111840;-0.035634;0.496534;
0.066559;0.014348;1.034269;-0.025565;0.025435;-0.442397;
0.023505;0.017217;1.039584;0.188176;0.017802;0.435466;
0.055361;0.044098;1.021545;-0.101901;-0.043267;-0.175221;
0.043743;0.003905;1.029134;0.188176;0.201008;0.175924;
0.049757;0.047816;1.027650;-0.056099;-0.241740;0.244626;
0.045252;0.000755;1.025431;-0.178237;0.086504;-0.075985;
0.027396;0.022492;1.037264;0.165275;0.063603;0.336229;
0.058740;0.009087;1.016916;-0.445412;-0.050900;-0.327893;
0.033783;0.015829;1.027204;0.180542;0.040702;0.557603;
0.046681;0.039863;1.027491;-0.056099;0.048336;-0.480565;
0.035657;-0.000213;1.024300;0.150008;0.002534;0.130122;
0.034477;0.043722;1.014867;-0.079000;-0.058534;0.153023;
0.051038;-0.000451;1.023779;-0.086634;0.071237;-0.167588;
0.039333;0.038350;1.031779;-0.117168;-0.104336;0.122489;
0.065448;0.010897;1.018509;-0.094267;0.063603;-0.404229;
0.023754;0.018855;1.033972;0.195809;-0.104336;0.565237;
0.064767;0.025825;1.041522;-0.185870;-0.005099;-0.503466;
0.022312;0.011130;1.027218;0.157641;0.086504;0.359130;
0.055674;0.022788;1.030558;-0.170603;-0.081435;-0.373695;
0.037174;-0.001482;1.032641;0.195809;-0.050900;0.343863;
0.042492;0.047088;1.035383;0.195809;-0.111969;-0.190489;
0.057457;-0.000786;1.029751;-0.162970;0.338412;0.084321;
0.039117;0.040223;1.027143;0.088939;-0.241740;0.214092;
0.052397;0.006259;1.028065;0.035504;-0.005099;-0.259191;
0.020734;0.016523;1.017710;0.150008;-0.111969;0.290428;
0.054819;0.020519;1.011386;-0.216405;-0.173038;-0.534000;
0.019227;-0.000097;1.019900;0.386649;-0.081435;0.389664;
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

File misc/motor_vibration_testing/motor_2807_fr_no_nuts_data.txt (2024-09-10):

-0.001916;0.030665;1.009257;0.171168;0.011783;-0.208260;
0.062911;0.048625;1.039619;0.071931;-0.270660;0.226855;
0.084799;0.007639;1.015058;0.148267;0.332394;-0.025053;
0.061069;0.020969;1.038456;-0.080741;0.126287;-0.192992;
-0.022881;0.015547;0.995007;0.423076;-0.316462;-0.101389;
0.078338;0.033105;1.061192;-0.088374;0.034684;0.142885;
0.071276;0.005314;1.017530;-0.370817;0.072852;-0.139557;
-0.012934;0.006641;1.003356;0.354374;-0.186691;-0.131924;
0.074120;0.032847;1.057450;-0.141809;-0.217225;0.173420;
0.084406;0.000054;1.031372;-0.294481;0.469798;0.005481;
0.039044;0.037346;1.013859;0.003229;0.278958;-0.147191;
0.005880;0.032656;1.036616;0.316206;-0.247759;-0.040321;
0.067214;0.018005;1.015204;-0.080741;0.118653;0.226855;
0.082700;0.012513;1.005045;-0.263947;0.294226;-0.223527;
-0.007281;0.025778;1.009600;0.285671;-0.171423;-0.086122;
0.062719;0.044962;1.056729;-0.103642;-0.133255;0.142885;
0.101287;0.008956;1.000353;-0.172344;0.210256;0.043649;
-0.003000;0.016816;1.033072;0.186435;0.019416;-0.177725;
0.000245;0.013075;1.033309;0.102465;-0.324095;0.211588;
0.086035;0.032386;1.036279;-0.424252;0.156821;0.135252;
0.075585;0.017988;1.019737;-0.210512;-0.011118;-0.170092;
-0.023232;0.006385;1.020127;0.346740;-0.201958;0.028382;
0.067901;0.038707;1.028266;-0.080741;-0.179057;0.280290;
0.073489;0.010527;0.999736;-0.309748;0.271325;-0.147191;
0.023978;0.031183;1.042737;0.064297;-0.011118;-0.261695;
0.016049;0.027676;1.029086;0.026129;-0.362263;0.097084;
0.084865;0.007691;1.001572;-0.195245;0.111020;0.119985;
0.033718;0.021591;1.038076;-0.057840;-0.117988;-0.147191;
-0.005518;0.012897;1.023415;0.308572;-0.194324;0.005481;
0.069786;0.055017;1.037112;-0.088374;0.049951;0.081817;
0.104782;0.007356;1.029806;-0.286848;0.126287;-0.147191;
-0.022877;0.026267;1.011347;0.331473;0.004149;-0.231160;
0.056745;0.058055;1.037952;0.148267;-0.385164;0.051282;
0.080512;0.034067;1.019304;-0.325016;0.248424;0.051282;
0.063908;0.024286;1.055955;-0.118909;0.103386;-0.185359;
-0.011192;0.016967;0.986611;0.239870;-0.377530;0.104718;
0.087930;0.031503;1.053213;0.049030;0.065218;0.356626;
0.090018;0.003083;1.019725;-0.225779;0.301859;-0.162458;
-0.001606;0.025185;1.033949;0.148267;0.049951;-0.139557;
0.042935;0.044494;1.023091;0.239870;-0.163790;0.188687;
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

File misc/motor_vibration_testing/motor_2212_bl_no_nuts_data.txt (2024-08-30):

0.050010;0.060136;1.002084;0.095305;-0.180285;0.028649;
0.049276;0.062670;1.011184;-0.187138;-0.012347;-0.093488;
0.062449;0.054637;1.001691;0.057137;0.041089;-0.101122;
0.050461;0.046177;1.013168;0.011336;0.025821;0.104985;
0.052587;0.044577;1.013421;0.064771;-0.004713;0.104985;
0.065037;0.059789;1.012102;-0.255840;-0.004713;-0.169824;
0.050962;0.051793;1.012031;-0.011565;0.109791;-0.032420;
0.039649;0.041432;1.007796;0.232710;-0.103950;0.104985;
0.052298;0.049635;1.010057;-0.034466;-0.073415;-0.101122;
0.046200;0.062401;1.019719;-0.194771;0.292997;-0.062954;
0.048380;0.032707;1.015886;0.209809;0.010554;0.021015;
0.057589;0.043746;1.006613;-0.065000;-0.233721;-0.062954;
0.053165;0.058173;1.007496;-0.057367;0.002921;-0.009519;
0.036913;0.057553;1.019026;0.072404;0.086890;0.066817;
0.051587;0.043582;1.015354;0.164007;-0.134484;-0.070588;
0.061995;0.047219;1.012857;0.041870;0.354066;0.089718;
0.049205;0.055623;1.013043;0.110572;-0.210820;-0.009519;
0.047635;0.054074;1.029182;0.186908;0.010554;0.005748;
0.074622;0.058661;1.020068;-0.087901;-0.096316;-0.024786;
0.045050;0.044253;0.999331;0.041870;-0.027614;0.089718;
0.048328;0.055435;1.002973;-0.187138;-0.096316;-0.177458;
0.052717;0.056109;1.018004;0.049504;0.002921;0.181321;
0.060006;0.055240;1.017850;-0.057367;-0.019980;-0.001885;
0.049592;0.042986;1.014581;0.263244;-0.096316;0.089718;
0.048535;0.048204;1.008021;-0.003931;0.117424;0.097351;
0.051339;0.059148;1.013614;-0.110802;0.010554;-0.124023;
0.067842;0.061427;1.014863;0.041870;-0.019980;-0.009519;
0.055829;0.039908;1.016832;0.240343;0.094524;0.082084;
0.053266;0.049438;1.010068;-0.057367;-0.035247;0.066817;
0.049816;0.064601;1.008032;-0.210038;0.231929;0.013382;
0.058006;0.048113;1.003740;0.393015;-0.065782;-0.017153;
0.049486;0.039609;1.000553;0.164007;-0.050514;-0.032420;
0.063378;0.053703;1.001445;-0.240573;-0.149751;-0.017153;
0.043235;0.042673;0.997321;0.087672;-0.279522;-0.032420;
0.048683;0.049289;1.015150;0.095305;-0.157385;-0.040053;
0.059020;0.043080;1.006379;0.125840;0.071623;-0.169824;
0.056531;0.045720;1.011777;-0.019199;0.048722;-0.047687;
0.040618;0.056354;1.008027;0.087672;-0.142118;0.005748;
0.055242;0.058161;1.016598;-0.026832;-0.096316;-0.124023;
0.059187;0.049998;1.012122;0.026603;0.041089;-0.001885;
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

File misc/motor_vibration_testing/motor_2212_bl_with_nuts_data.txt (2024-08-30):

0.047998;0.057900;1.005947;-0.049733;-0.241354;-0.032420;
0.078067;0.054422;1.018830;0.034236;-0.180285;-0.108756;
0.058046;0.051883;1.011397;0.095305;-0.203186;-0.062954;
0.056242;0.063115;1.018646;-0.026832;-0.187919;0.074450;
0.060580;0.066051;1.021693;-0.110802;-0.073415;0.051550;
0.061029;0.037184;1.013433;0.209809;0.125058;0.051550;
0.061736;0.054876;1.020566;-0.065000;-0.226087;0.021015;
0.062041;0.072388;1.016656;-0.095535;0.102157;0.082084;
0.055261;0.045149;1.010279;0.034236;0.262463;-0.139290;
0.051533;0.053294;1.012797;0.095305;-0.210820;-0.040053;
0.053969;0.053880;1.028288;0.018969;-0.119217;0.104985;
0.059093;0.047117;1.015512;-0.065000;0.056356;-0.017153;
0.048402;0.051344;1.023268;-0.042099;-0.111583;-0.032420;
0.053713;0.062429;0.996530;0.141107;-0.088682;0.051550;
0.066197;0.039312;1.008388;0.087672;0.048722;-0.131656;
0.058917;0.052759;1.018534;-0.087901;-0.050514;-0.108756;
0.046699;0.062202;1.021195;0.064771;0.048722;0.043916;
0.067893;0.058451;1.011142;-0.019199;0.010554;0.043916;
0.064706;0.039218;1.006894;0.148740;-0.012347;-0.116389;
0.052163;0.045783;1.013922;0.102939;-0.203186;-0.009519;
0.043526;0.061811;1.004714;-0.202405;-0.027614;-0.070588;
0.075049;0.062344;1.020373;-0.065000;0.025821;0.074450;
0.044091;0.037721;1.006089;0.072404;-0.187919;0.082084;
0.049696;0.060764;1.012879;-0.095535;-0.332957;-0.017153;
0.060869;0.057498;1.019366;0.156374;-0.027614;0.166053;
0.069018;0.045620;1.013669;0.156374;-0.241354;-0.017153;
0.049112;0.045521;1.006028;0.003702;-0.027614;-0.185092;
0.063838;0.055567;1.010797;-0.065000;0.071623;0.028649;
0.063229;0.054740;1.023038;0.034236;-0.058148;0.028649;
0.053263;0.058510;1.013633;0.041870;-0.378759;0.089718;
0.059866;0.054858;1.008769;-0.011565;-0.096316;-0.032420;
0.062917;0.037916;1.024015;0.110572;-0.035247;-0.246160;
0.050723;0.048293;1.006827;-0.171870;0.048722;0.028649;
0.048595;0.059661;1.007698;0.003702;-0.065782;0.005748;
0.067039;0.049231;1.017126;0.385382;0.102157;0.036283;
0.056865;0.042795;1.010758;0.102939;0.216661;0.028649;
0.044459;0.046476;1.020199;0.003702;-0.126850;-0.040053;
0.066579;0.064126;1.020279;-0.118435;-0.027614;0.005748;
0.065143;0.044533;1.002073;-0.019199;-0.050514;0.097351;
0.057746;0.041347;1.008788;-0.118435;-0.027614;-0.070588;
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

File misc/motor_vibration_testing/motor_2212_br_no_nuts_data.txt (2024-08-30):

0.059047;0.049153;1.004751;-0.015618;-0.318894;-0.020748;
0.051031;0.053489;1.011076;0.274458;-0.074619;0.139557;
0.057197;0.036839;1.002339;0.144687;-0.150955;0.032687;
0.062011;0.055384;1.021068;0.030183;-0.089886;0.086122;
0.058258;0.056049;1.012196;0.030183;-0.028818;-0.013114;
0.054191;0.052922;1.011848;0.221023;0.047518;0.093756;
0.061282;0.043943;1.007895;0.030183;-0.128054;-0.043649;
0.052207;0.067919;1.010321;-0.221725;-0.036451;-0.058916;
0.055415;0.057169;1.014870;-0.076687;-0.021184;0.147191;
0.054147;0.046367;1.013959;-0.007985;-0.265459;-0.203954;
0.059566;0.058745;1.008821;0.167588;-0.173856;0.124290;
0.053766;0.059474;1.011201;0.014916;0.085686;0.009786;
0.055370;0.066660;1.013781;0.106519;-0.227291;0.063221;
0.055606;0.053396;1.006235;0.205756;-0.082253;-0.097084;
0.058510;0.050488;1.014571;0.037817;0.001717;-0.051282;
0.051991;0.057473;1.013599;0.060718;-0.036451;-0.074183;
0.052378;0.072041;1.008176;0.129420;-0.112787;0.101389;
0.049632;0.047219;1.020528;0.121786;-0.066986;-0.043649;
0.054327;0.039803;1.014602;0.152321;0.001717;0.040321;
0.052391;0.062536;1.025204;0.068351;0.078053;-0.058916;
0.048104;0.062203;1.016556;0.129420;-0.112787;-0.104717;
0.050815;0.041402;1.002069;0.098885;0.016984;0.002153;
0.059618;0.056716;1.020072;0.098885;-0.135688;0.086122;
0.042783;0.059912;1.010807;-0.030886;-0.074619;-0.013114;
0.059107;0.052712;1.014612;0.213389;-0.234925;0.139557;
0.053565;0.045317;1.010748;0.129420;-0.066986;-0.081817;
0.055097;0.062660;1.007833;-0.069053;0.085686;-0.112351;
0.049987;0.058740;1.023643;-0.153023;0.078053;-0.097084;
0.053438;0.056592;1.015324;0.060718;0.001717;-0.074183;
0.045744;0.044959;1.012103;0.129420;0.016984;-0.173420;
0.061209;0.060624;1.015247;-0.038519;-0.181489;0.063221;
0.057061;0.055556;1.015850;0.091252;-0.196757;0.002153;
0.055752;0.054249;1.014096;0.159954;-0.028818;-0.089450;
0.054799;0.047491;1.022077;0.053084;0.016984;0.032687;
0.052398;0.060903;1.013410;-0.007985;0.070419;-0.028382;
0.053897;0.064963;1.019375;-0.099588;0.093320;-0.036015;
0.049972;0.055229;1.016971;0.236290;-0.166222;-0.127618;
0.052662;0.066051;1.014469;-0.206458;-0.044085;0.177725;
0.072043;0.061204;1.019088;0.106519;0.047518;0.009786;
0.047825;0.065650;1.019789;0.060718;0.009350;-0.043649;
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

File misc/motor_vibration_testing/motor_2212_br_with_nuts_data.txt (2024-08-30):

0.058238;0.063944;1.018686;-0.038519;0.078053;0.032687;
0.050426;0.046603;1.009005;0.045450;-0.021184;-0.043649;
0.061769;0.053502;1.009757;0.121786;0.055152;0.124290;
0.053466;0.062917;1.031110;-0.000351;0.009350;0.040321;
0.045854;0.058323;1.008620;0.091252;-0.341795;-0.051282;
0.040301;0.024619;0.989415;0.068351;-0.196757;0.139557;
0.048328;0.057057;0.997112;-0.175924;-0.158589;-0.158153;
0.050430;0.062903;1.023465;-0.099588;-0.021184;0.147191;
0.047515;0.050682;1.014173;0.167588;-0.112787;-0.081817;
0.067076;0.052516;1.008102;-0.061420;-0.036451;0.093756;
0.044192;0.063412;1.012104;-0.107221;0.146755;-0.097084;
0.058485;0.066507;1.009654;0.129420;0.055152;0.124290;
0.053775;0.039712;1.010179;0.320260;-0.005917;-0.097084;
0.056366;0.065333;1.019906;-0.175924;0.085686;0.032687;
0.057583;0.053992;1.023927;0.037817;-0.013551;-0.104717;
0.044874;0.056653;1.014467;0.075985;-0.097520;-0.066550;
0.047852;0.059385;1.007928;0.106519;-0.066986;-0.119985;
0.047265;0.051592;1.010504;0.045450;0.169656;-0.119985;
0.050810;0.067463;1.017161;-0.076687;-0.120421;-0.058916;
0.040677;0.046416;1.011807;-0.030886;-0.074619;0.109023;
0.062244;0.050015;1.003092;-0.076687;-0.021184;0.025054;
0.042922;0.054462;1.004354;-0.153023;0.047518;-0.043649;
0.051101;0.067060;1.022063;-0.007985;-0.089886;-0.066550;
0.045916;0.047229;1.016797;0.159954;-0.005917;0.025054;
0.066420;0.058627;1.028289;-0.244626;0.032251;0.139557;
0.052460;0.057493;1.030281;0.129420;-0.051718;0.040321;
0.035159;0.043006;1.013641;0.121786;0.016984;-0.005481;
0.054725;0.058804;1.012186;0.198122;-0.189123;0.109023;
0.045846;0.056923;1.013014;-0.061420;-0.181489;-0.051282;
0.049918;0.071004;1.028970;0.014916;-0.112787;0.101389;
0.052643;0.045796;1.013194;0.106519;0.223091;0.032687;
0.052849;0.055072;1.013332;-0.099588;-0.089886;0.055588;
0.045583;0.060851;1.015764;-0.069053;0.078053;-0.173420;
0.059365;0.061581;1.020139;0.098885;0.039885;0.063221;
0.056412;0.043275;1.011739;0.068351;0.016984;-0.058916;
0.055345;0.066400;1.012796;-0.183557;-0.005917;0.170092;
0.049020;0.057530;1.010615;0.075985;-0.044085;-0.135252;
0.057396;0.053328;1.012390;0.022550;-0.227291;-0.051282;
0.064897;0.052205;1.010763;0.098885;-0.013551;0.101389;
0.044500;0.058144;1.017671;0.144687;-0.173856;-0.058916;
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

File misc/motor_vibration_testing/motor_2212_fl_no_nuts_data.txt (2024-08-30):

0.035299;0.057810;1.025383;0.035763;0.055007;-0.050412;
0.026446;0.049431;1.015082;0.119733;0.077908;0.117527;
0.033347;0.041659;1.010898;-0.002405;0.009206;-0.050412;
0.024491;0.043067;1.019866;-0.078740;0.108443;-0.103847;
0.031909;0.059077;1.023146;-0.063473;0.009206;-0.096214;
0.028178;0.045575;1.012353;0.005229;-0.082397;0.071725;
0.033790;0.037443;1.004467;-0.017672;0.009206;-0.142015;
0.026918;0.041057;1.007610;-0.078740;0.024473;-0.096214;
0.040249;0.056460;1.016606;-0.147443;0.138977;-0.119115;
0.023194;0.046425;1.020387;0.211336;-0.196901;0.155695;
0.029407;0.038417;1.002212;-0.094008;0.062641;-0.134382;
0.023516;0.055576;1.011451;0.043397;-0.128199;0.041191;
0.025090;0.056685;1.015413;-0.063473;-0.105298;0.086992;
0.031574;0.044545;1.014103;-0.086374;-0.090031;-0.050412;
0.018967;0.043590;1.007043;-0.055840;-0.059496;-0.012244;
0.027626;0.051779;1.021753;-0.055840;0.253481;0.010656;
0.034610;0.048980;1.024019;-0.078740;-0.090031;0.041191;
0.027404;0.047139;1.021928;0.272405;-0.082397;-0.019878;
0.027753;0.044463;1.021158;-0.216145;0.009206;-0.058046;
0.022064;0.043437;1.019837;0.020496;-0.044229;-0.080947;
0.045419;0.056040;1.020842;-0.185611;-0.120565;0.010656;
0.025991;0.041298;1.010543;0.058664;-0.067130;-0.080947;
0.040535;0.037458;1.033499;-0.055840;0.001572;-0.210718;
0.037399;0.051993;1.020669;-0.277214;-0.090031;0.148061;
0.038857;0.058326;1.015387;-0.048206;-0.174000;-0.073313;
0.034286;0.042359;1.005527;0.127366;0.032107;-0.134382;
0.028941;0.040775;1.031911;-0.071107;0.161877;0.010656;
0.022087;0.056030;1.030810;-0.025305;0.047374;0.079359;
0.023670;0.044794;1.007128;0.127366;-0.059496;0.003023;
0.018369;0.039511;1.013597;0.012863;0.062641;0.079359;
0.035394;0.051386;1.019161;-0.216145;-0.067130;-0.004611;
0.023725;0.056495;1.023728;-0.177977;0.093175;0.140427;
0.016067;0.038374;1.010114;-0.032939;0.047374;-0.119115;
0.014506;0.031466;1.009747;0.188435;-0.120565;0.102259;
0.020077;0.038428;1.017284;-0.139809;0.039740;0.064092;
0.033310;0.051390;1.009567;-0.216145;0.177145;0.033557;
0.016163;0.038244;1.017716;-0.002405;0.070275;-0.073313;
0.021649;0.029283;1.003441;0.150267;-0.097664;-0.103847;
0.032907;0.049123;1.005850;-0.109275;0.032107;0.071725;
0.033532;0.050451;1.011273;0.035763;0.108443;0.117527;
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

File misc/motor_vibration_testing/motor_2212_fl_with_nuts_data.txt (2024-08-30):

0.026500;0.042037;1.009335;0.081565;-0.257970;-0.172550;
0.026988;0.041131;1.012516;0.028130;-0.105298;0.003023;
0.029186;0.047989;1.024173;-0.116908;0.291649;0.125160;
0.035126;0.046464;1.016878;-0.040572;-0.021328;0.125160;
0.039113;0.053465;1.015565;0.066298;0.230580;0.056458;
0.056034;0.058027;1.021512;0.028130;-0.097664;-0.065679;
0.019673;0.046162;1.013957;-0.010038;-0.036596;0.003023;
0.028262;0.046823;1.014089;-0.116908;-0.349573;0.018290;
0.022011;0.037105;1.020480;0.051031;0.024473;0.018290;
0.041242;0.047910;1.012082;-0.010038;0.001572;0.148061;
0.024669;0.051599;1.002336;-0.071107;0.131343;-0.027512;
0.030413;0.045945;1.013616;-0.032939;-0.303771;-0.035145;
0.024754;0.018655;0.999897;0.051031;-0.120565;0.071725;
0.033229;0.041533;1.002557;-0.071107;-0.219802;0.056458;
0.027704;0.058833;1.020386;-0.139809;0.077908;0.056458;
0.027167;0.053411;1.018092;0.028130;0.024473;-0.119115;
0.022923;0.032194;1.015026;0.028130;0.161877;0.086992;
0.025175;0.043743;1.013755;0.051031;0.062641;-0.050412;
0.021132;0.043885;1.003400;0.135000;0.123710;-0.080947;
0.039807;0.060214;1.024746;0.142634;-0.044229;-0.035145;
0.025345;0.047884;1.029757;-0.147443;-0.326672;0.064092;
0.032562;0.043675;1.018027;-0.094008;0.108443;0.048824;
0.030202;0.061552;1.014575;-0.078740;0.276381;0.071725;
0.018732;0.051987;1.032175;0.096832;-0.044229;0.079359;
0.018780;0.042482;1.015362;-0.094008;0.032107;-0.088580;
0.028725;0.043092;1.007420;-0.032939;-0.051863;0.041191;
0.037034;0.055346;1.017770;-0.101641;0.032107;0.041191;
0.038912;0.062344;1.023293;-0.055840;0.100809;0.064092;
0.031613;0.038080;1.022102;-0.002405;0.047374;-0.042779;
0.028973;0.040327;1.017683;-0.109275;0.016840;0.064092;
0.043386;0.055404;1.017371;-0.155076;0.070275;-0.149649;
0.033266;0.049276;1.032096;0.035763;0.024473;0.056458;
0.028237;0.037258;1.010271;0.073931;-0.235069;-0.050412;
0.032408;0.041193;1.015537;0.180802;0.047374;-0.050412;
0.040045;0.058578;1.011974;-0.109275;-0.181634;0.041191;
0.036842;0.047958;1.030166;-0.132176;0.230580;0.132794;
0.025803;0.030863;0.997637;0.058664;0.184778;-0.042779;
0.032388;0.036287;1.013504;-0.071107;-0.059496;0.079359;
0.035817;0.068328;1.026034;-0.132176;-0.013695;-0.065679;
0.035131;0.059039;1.026625;0.073931;0.009206;-0.187817;
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

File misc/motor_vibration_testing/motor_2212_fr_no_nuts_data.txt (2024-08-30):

0.045649;0.062543;1.014564;0.194031;-0.171276;-0.130695;
0.018320;0.039459;1.010162;0.209298;-0.270513;-0.061992;
0.035664;0.059322;1.010697;-0.103679;-0.064406;0.044878;
0.033510;0.052994;1.018667;0.247466;0.004296;-0.145962;
0.036165;0.058895;1.013150;0.270367;-0.224711;0.075412;
0.034465;0.053479;1.015254;-0.004443;-0.148376;-0.008557;
0.052651;0.064881;1.017885;0.087160;-0.094940;0.021977;
0.049769;0.055262;1.019911;0.125328;-0.178910;-0.153595;
0.036636;0.051927;1.018696;-0.042611;-0.003337;0.090679;
0.027342;0.056611;1.019613;0.026092;-0.278147;-0.031458;
0.047734;0.068816;1.019834;-0.034977;0.034831;0.189916;
0.047731;0.059969;1.015046;0.071893;-0.209444;-0.184130;
0.030033;0.039282;1.009345;0.262733;-0.278147;0.243351;
0.046478;0.056636;1.024789;-0.111313;-0.125475;0.098313;
0.054066;0.057228;1.023434;0.033725;-0.156009;0.144115;
0.057794;0.067464;1.027559;-0.004443;-0.064406;0.098313;
0.030505;0.042550;1.014549;-0.027343;-0.247612;-0.107794;
0.048238;0.060475;1.014571;-0.057878;-0.033872;0.075412;
0.036120;0.062109;1.016384;-0.080778;-0.163643;0.021977;
0.034236;0.053715;1.015500;0.125328;-0.056772;-0.008557;
0.025029;0.046387;1.011584;0.048993;-0.140742;-0.138328;
0.041925;0.066271;1.015056;-0.065511;-0.323948;0.167015;
0.045776;0.053605;1.019831;0.178764;0.065365;-0.092527;
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

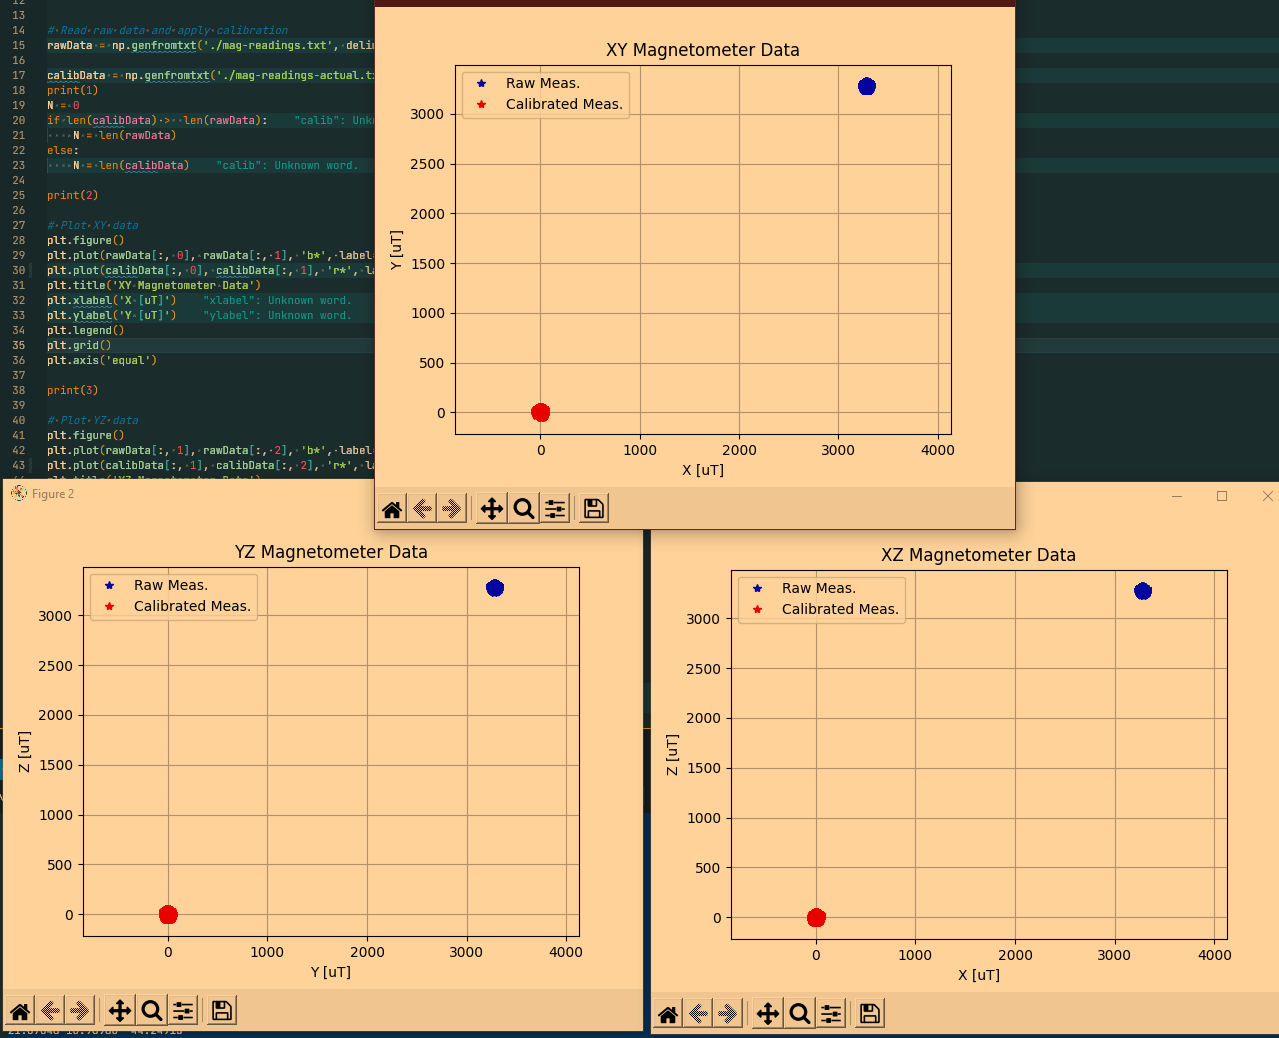
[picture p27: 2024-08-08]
images/Magnetometer_calibrated_2.png

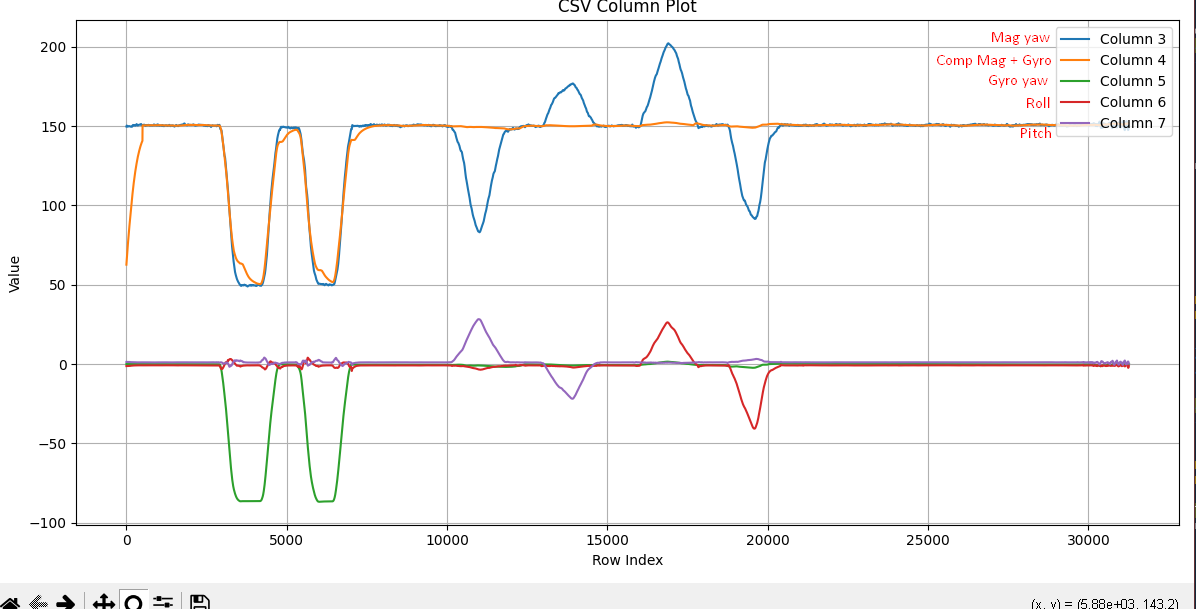
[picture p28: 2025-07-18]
images/yaw compelentary filter testing.png

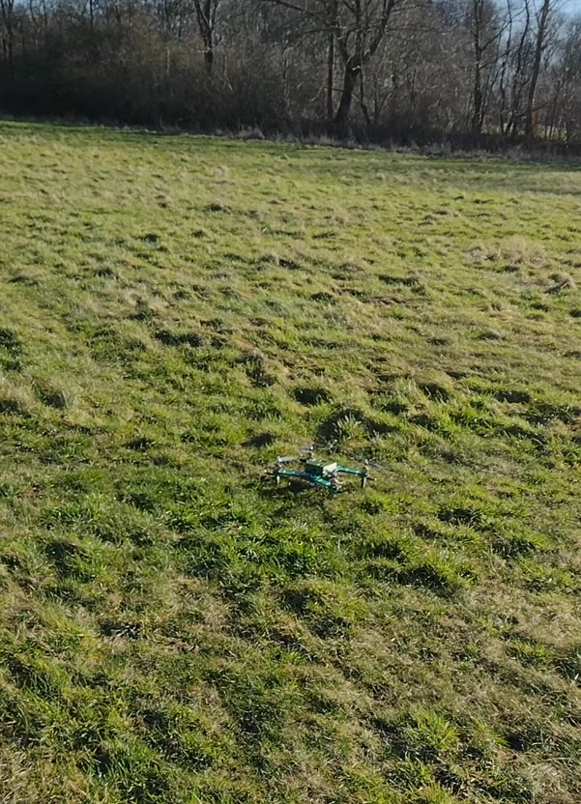
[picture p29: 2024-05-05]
images/test3_image.png

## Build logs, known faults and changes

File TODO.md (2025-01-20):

# TODO LIST FOR THE PROJECT

* X Fix issues with logger
* X Yaw low pass filtering
* X Implement rmp filtering
* X Tie down loose parts
* X D term biquad filtering at 75Hz to 100Hz based on throttle 0% to 100%. AOS style filter
* X Filter accelerometer
* X Acro mode tuning using PID toolbox
* X Angle mode tuning
* Implement GPS position hold
* Implement altitude hold using vertical acceleration
* ELRS RX TX
* Dynamic idle (Optional)

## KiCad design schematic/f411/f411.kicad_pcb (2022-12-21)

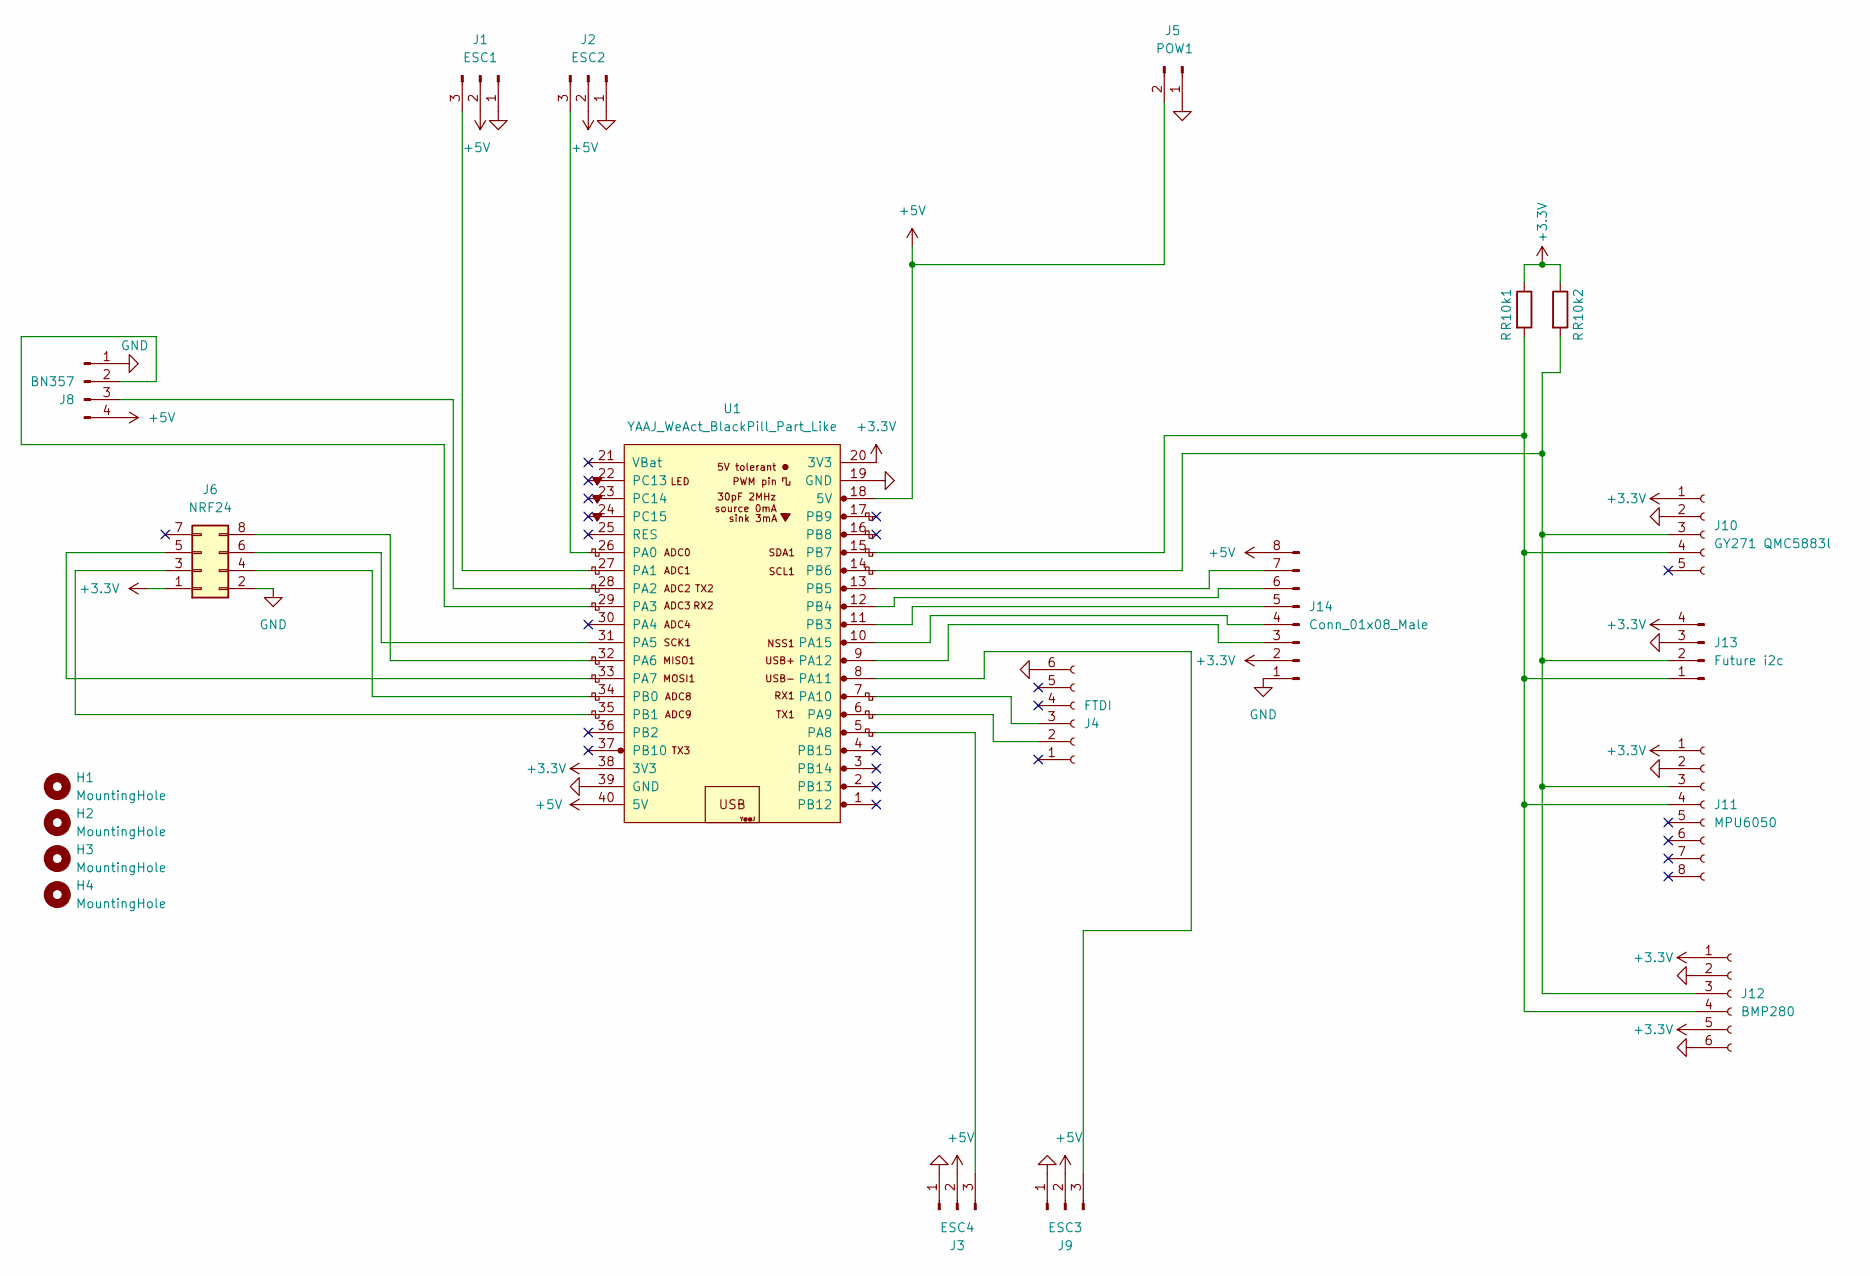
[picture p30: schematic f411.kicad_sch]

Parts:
H1, H2, H3, H4: MountingHole; MountingHole_4.3mm_M4
J1: ESC1; PinHeader_1x03_P2.54mm_Vertical
J2: ESC2; PinHeader_1x03_P2.54mm_Vertical
J3: ESC4; PinHeader_1x03_P2.54mm_Vertical
J4: FTDI; PinSocket_1x06_P2.54mm_Vertical
J5: POW1; PinHeader_1x02_P2.54mm_Vertical
J6: NRF24; PinSocket_2x04_P2.54mm_Vertical
J8: BN357; PinHeader_1x04_P2.54mm_Vertical
J9: ESC3; PinHeader_1x03_P2.54mm_Vertical
J10: GY271 QMC5883l; PinSocket_1x05_P2.54mm_Vertical
J11: MPU6050; PinSocket_1x08_P2.54mm_Vertical
J12: BMP280; PinSocket_1x06_P2.54mm_Vertical
J13: Future i2c; PinHeader_1x04_P2.54mm_Vertical
J14: Conn_01x08_Male; PinHeader_1x08_P2.54mm_Vertical
R10k1, R10k2: R; R_Axial_DIN0207_L6.3mm_D2.5mm_P10.16mm_Horizontal
U1: YAAJ_WeAct_BlackPill_Part_Like; YAAJ_WeAct_BlackPill_2

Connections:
+3.3V: J6.1, J10.1, J11.1, J12.1, J12.5, J13.4, J14.2, R10k1.1, R10k2.1, U1.20 (3V3), U1.38 (3V3)
+5V: J1.2, J2.2, J3.2, J5.2, J8.4, J9.2, J14.8, U1.18 (5V), U1.40 (5V)
GND: J1.1, J2.1, J3.1, J4.6, J5.1, J6.2, J8.1, J9.1, J10.2, J11.2, J12.2, J12.6, J13.3, J14.1, U1.19 (GND), U1.39 (GND)
unnamed: J1.3, U1.27 (PA1)
unnamed: J2.3, U1.26 (PA0)
unnamed: J3.3, U1.5 (PA8)
unnamed: J4.2, U1.6 (PA9)
unnamed: J4.3, U1.7 (PA10)
unnamed: J8.2, U1.29 (PA3)
unnamed: J8.3, U1.28 (PA2)
unnamed: J9.3, U1.8 (PA11)
unnamed: J10.3, J11.3, J12.3, J13.2, R10k2.2, U1.14 (PB6)
unnamed: J10.4, J11.4, J12.4, J13.1, R10k1.2, U1.15 (PB7)
unnamed: J14.3, U1.9 (PA12)
unnamed: J14.4, U1.10 (PA15)
unnamed: J14.5, U1.11 (PB3)
unnamed: J14.6, U1.12 (PB4)
unnamed: J14.7, U1.13 (PB5)
unnamed: J6.6, U1.31 (PA5)
unnamed: J6.8, U1.32 (PA6)
unnamed: J6.5, U1.33 (PA7)
unnamed: J6.4, U1.34 (PB0)
unnamed: J6.3, U1.35 (PB1)

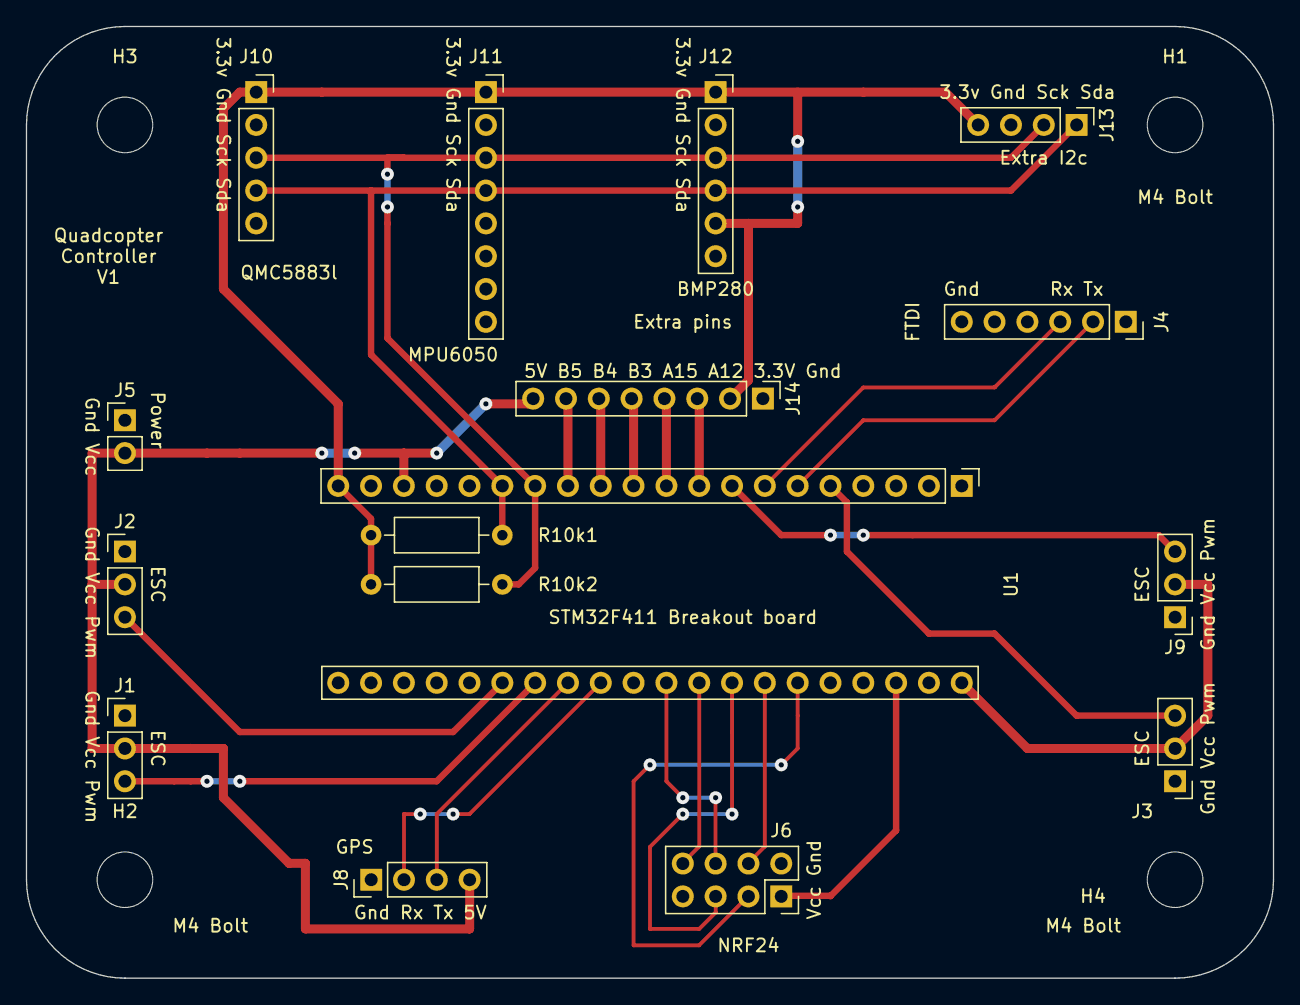
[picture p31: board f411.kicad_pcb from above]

Board: 2 copper layers, 96.5 x 73.7 mm, 20 parts (0 on the bottom side), 23 nets.

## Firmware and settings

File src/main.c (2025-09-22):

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
/* Includes ------------------------------------------------------------------*/
#include "main.h"

/* USER CODE BEGIN Includes */
#include "system.h"
#include "../lib/utils/reset_i2c/reset_i2c.h"
#include "../lib/printf/retarget.h"
#include "../lib/.layers/common.h"

/* USER CODE END Includes */

I2C_HandleTypeDef hi2c1;

SPI_HandleTypeDef hspi1;
SPI_HandleTypeDef hspi3;
DMA_HandleTypeDef hdma_spi3_tx;

TIM_HandleTypeDef htim3;

UART_HandleTypeDef huart1;
UART_HandleTypeDef huart2;
DMA_HandleTypeDef hdma_usart2_rx;

/* USER CODE BEGIN PV */
TIM_HandleTypeDef htim4;

/* USER CODE END PV */

void SystemClock_Config(void);
static void MX_GPIO_Init(void);
static void MX_DMA_Init(void);
static void MX_USART1_UART_Init(void);
static void MX_I2C1_Init(void);
static void MX_USART2_UART_Init(void);
static void MX_SPI1_Init(void);
static void MX_SPI3_Init(void);
static void MX_TIM3_Init(void);
/* USER CODE BEGIN PFP */
static void MX_TIM4_Init(void);
/* USER CODE END PFP */

/**
  * @brief  The application entry point.
  * @retval int
  */
int main(void)
{
  /* MCU Configuration--------------------------------------------------------*/

  /* Reset of all peripherals, Initializes the Flash interface and the Systick. */
  HAL_Init();

  /* Configure the system clock */
  SystemClock_Config();

  /* Initialize all configured peripherals */
  MX_GPIO_Init();
  MX_DMA_Init();
  MX_USART1_UART_Init();
  MX_I2C1_Init();
  MX_USART2_UART_Init();
  MX_SPI1_Init();
  MX_SPI3_Init();
  MX_TIM3_Init();
  /* USER CODE BEGIN 2 */
  MX_TIM4_Init();
  RetargetInit(&huart1);
//   I2C_Bus_Reset(GPIOB, GPIO_PIN_6, GPIOB, GPIO_PIN_7); // Check and reset the i2c slaves if they are fucked up after reflash or restart
//   MX_I2C1_Init();
  
  HAL_GPIO_WritePin(GPIOB, GPIO_PIN_4, GPIO_PIN_SET);
  HAL_GPIO_WritePin(GPIOB, GPIO_PIN_5, GPIO_PIN_SET);
  HAL_GPIO_WritePin(GPIOA, GPIO_PIN_15, GPIO_PIN_SET);

  // Initialize timer 4
  HAL_TIM_Base_Start(&htim4);

  /* USER CODE END 2 */

  /* Infinite loop */
  /* USER CODE BEGIN WHILE */
  return system_main();
  while (1)
  {
    /* USER CODE END WHILE */

    /* USER CODE BEGIN 3 */
  }
  /* USER CODE END 3 */
}

/* Auto generated shit again-----------------------------------------------*/

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


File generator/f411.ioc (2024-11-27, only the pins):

Mcu.UserName=STM32F411CEUx
PA0-WKUP.Signal=GPIO_Input
PA10.Signal=USART1_RX
PA12.Signal=GPXTI12
PA13.Signal=SYS_JTMS-SWDIO
PA14.Signal=SYS_JTCK-SWCLK
PA15.Signal=GPIO_Output
PA2.Signal=USART2_TX
PA3.Signal=USART2_RX
PA5.Signal=SPI1_SCK
PA6.Signal=SPI1_MISO
PA7.Signal=SPI1_MOSI
PA9.Signal=USART1_TX
PB0.Signal=GPIO_Output
PB1.Signal=GPIO_Output
PB3.Signal=SPI3_SCK
PB4.Signal=SPI3_MISO
PB5.Signal=SPI3_MOSI
PB6.Signal=I2C1_SCL
PB7.Signal=I2C1_SDA
PC13-ANTI_TAMP.Signal=GPIO_Output

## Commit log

2022-11-26 Added pwm and nrf24
2022-12-03 Added schematic and pcb
    [f411.kicad_pcb, f411.kicad_sch]
2022-12-21 Add error handling for uart 2
    [Pdb board v1.stl, Quadcopter parts v2.stl, Quadcopter v1.stl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]
2022-12-28 Add generator files and fixes for modules
    [main.c]
2023-03-02 Testing shit
    [GPS mount v3.stl, Pdb board v1.stl, Rotor leg v2.stl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]
2023-03-02 Fixing and simplifying bmp280 sensor values
    [main.c]
2023-03-04 Improve bmp280 and gy271 sensor drivers
2023-03-05 Fixing multiple sensors and cleaning up the drivers
    [main.c]
2023-04-23 Add pid abstraction
2023-05-08 Sensor fusion fix for accurate gyro and pid for upright position
    [main.c]
2023-05-08 Fix for sensor fusion again
    [main.c]
2023-05-08 Fix for sensor fusion again again
2023-05-16 Testing motor max min calibration
2023-05-18 Changes to pwm frequency
2023-05-21 Add testing pid settings
2023-12-20 Update code for first test flight with pid
2024-03-30 Working async sd data writing at 83 Hz
2024-04-28 SD logging at 139 Hz
2024-04-28 Initialized dma for async write but only sending 2 bytes with the rest zeros
2024-04-29 Changes that speed up sd to 234 Hz
2024-06-01 Fix led indicator
2024-06-04 Fix pwm value and 4 test
    [f411.ioc, main.c]
2024-07-29 Accelerometer calibration, new sensor fusion and data filtering
2024-07-30 Kalman filter altitude and vertical velocity
2024-08-05 Improving low-pass filtering of accelerometer and gyro data
2024-08-08 New magnetometer and corrected vertical velocity pid
    [Camera mount.stl, Case root.stl, Case top.stl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]
2024-08-12 Gps config and vibration testing
    [plot_data.py]
2024-08-14 Fixing roll, pitch and yaw values. Made yaw tilt compensation work
    [main.c, plot_data.py]
2024-08-14 Fix remote control inputs to motors
    [main.c]
2024-08-14 Fix initial state function
    [main.c]
2024-08-16 GPS PID adjustment
2024-08-27 Testing gps hold, before replacing the motors
2024-08-30 Old motor vibration testing
    [main.c, plot_data.py]
2024-09-10 Testing new motors
2024-09-17 New PID plan and flight test 18
2024-09-27 DSHOT600 and BlueJay
    [data3.csv]
2024-10-09 Add Bidirectional DSHOT600 functionality, fix issue with i2c freezing
    [f411.ioc, main.c]
2024-10-12 Fix bdshot600 with 100MHz system clock
    [main.c]
2024-10-14 520 Hz control loop
2024-10-15 Switch from milliseconds timing control to microseconds
2024-10-28 bdshot600 dma and performance optimizing
2024-11-27 RPM filtering and performance optimizing
    [1Quadcopter.csv, 24Quadcopter.csv, 4Quadcopter.csv]
2024-12-07 Fixing issue with changing accelerometer offsets freezing the controller
    [main.c]
2025-01-18 Angle mode testing done, gps testing not done
    [1Quadcopter.csv, 24Quadcopter.csv, 4Quadcopter.csv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]
2025-01-27 Add control over gps and altitude pid trough remote
2025-02-17 Fixes for altitude and gps before fligh 45
    [animate_gps_data.py, animate_gps_data_for_bad_data.py, compare_vertical_stabilization_stuff.py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]
2025-02-23 Swapped broken mpu6050, new gps hold roll pitch ratio
    [animate_gps_data2.py, animate_gps_data_for_bad_data.py, main.c]
2025-05-03 Simulator for gps logic and fix for gps logic
    [main.c, simulate_gps_logic.py]
2025-06-15 Latest code
    [10QuadYAW.csv, 11QuadYAW.csv, 12QuadYAW.csv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]
2025-07-18 New gps logic and new yaw sensor fusion
2025-08-21 Testing new magnetometers
2025-08-26 Add new magnetometer
2025-09-13 latest working magnetometer test with compass motor frequency calibration
2025-11-03 Latest mess in magnetometer
2025-11-04 Update mag calibrations
2025-11-21 Adjust calibration

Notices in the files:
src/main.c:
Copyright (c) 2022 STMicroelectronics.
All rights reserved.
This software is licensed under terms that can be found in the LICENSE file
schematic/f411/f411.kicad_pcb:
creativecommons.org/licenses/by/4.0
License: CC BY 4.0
